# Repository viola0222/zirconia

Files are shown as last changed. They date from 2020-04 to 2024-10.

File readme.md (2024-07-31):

## 概要
___

「zirconia v.2.0」はマイクロマウスのチャンピオンが製作したオープンソースのマイクロマウスをnakagawaが改訂した版です。
 
詳しい説明は、[こちらのリンクの資料](https://docs.google.com/presentation/d/1BjXeR3dtw2jEZHByvPkCKbgB9d2WKhvbEWPhUpI-utg/edit?usp=sharing)を参照してください。
  
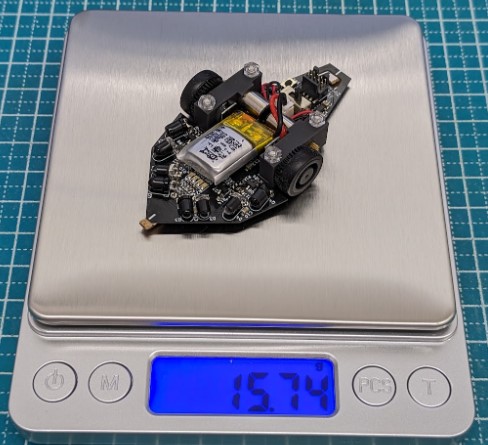
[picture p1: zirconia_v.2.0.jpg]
zirconia v.2.0


## 機能
___
 
各種インターフェースやセンサーの動作確認  

- マイコン各種機能(STM32F411)
- LED
- プッシュスイッチ
- モータ
- エンコーダ(MA730)
- IMU(ICM-42688-P)
- IRセンサ
  
機能の詳細についてはソフトマニュアルとサンプルコードのindex.hを参照して下さい。
 
## 動作環境
___
 
- 統合開発環境
    - STM32CubeIDE
    - Version :  1.15.0
    - URL : https://www.st.com/ja/development-tools/stm32cubeide.html
    - STM32CubeMX
    - Version :  6.10.0
    - URL : https://www.st.com/ja/development-tools/stm32cubemx.html    

- フラッシュライター
	- STM32CubeProgrammer
	- Version : 2.16.0
 	- URL : https://www.st.com/ja/development-tools/stm32cubeprog.html

※ Versionにはサンプルプログラムを開発したときのものを記載してあります。  
　　基本的には最新版をインストールすべきだと思いますが、  
　　サンプルプログラムが動かない等の不具合がありましたら参考にして下さい。

## 構成
___
 
- hardware
    - 回路図やガーバーデータ、部品リストなどハードウェアデータ
    - STEP 3D View https://a360.co/4cjsH3n
    
- software
    - CubeMXで自動生成したソフトと本サンプルプログラム
    - Incフォルダ内のIndex.hにサンプルプログラムの使い方が記載されています
    - Srcフォルダ内にmain.cなどのサンプルプログラムが入っています
- ハードマニュアル
    - ハードウェアの作り方や構成について記載されています
- ソフトマニュアル
    - サンプルプログラムの導入や使い方について記載されていますS
 
## その他
 ___

__本サンプルコードではマイクロマウスとして迷路を完走させることはできません。__  
本サンプルコードの目的は、製作したハードウェアの動作確認であり、その副産物として、マイクロマウスとして使いやすいデバイスドライバが書かれています。  
  
あくまでもzirconiaは動くハードウェアを用意しただけなので、ソフトウェアは自力で頑張れる人向けです。電子工作やプログラミングのガチ初心者にはオススメしません。  
電子工作や組み込みプログラム入門として、マイクロマウスを始める場合には(株)アールティより販売されている学習キット[Pi:Co Classic3.4 ESP32-S3](https://rt-net.jp/products/pico-classic3-esp32)や[Pi:Co V2](https://rt-net.jp/products/pico-v2)がオススメです。
 
## 作者
___
 
[Noriaki Nakagawa](https://github.com/noriakinakagawa)  
zirconia_sample is licensed under the Apache License, Version2.0

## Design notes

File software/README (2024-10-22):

# ビルド方法
## make

```bash
make
```

## clangd

- 次の内容の `compile_flags.txt` を作成することで、clangd による補完が動作するようになる

```
-I./arm-gnu-toolchain-13.2.Rel1-x86_64-arm-none-eabi/arm-none-eabi/include
```

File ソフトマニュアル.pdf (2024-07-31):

# 開発環境構築

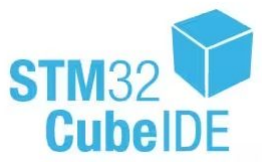
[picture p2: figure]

ま、下記ソフトをインストールしま。

① 統合開発環境

STM32CubeIDE

Version : 1.15.0

URL : https://www.st.com/ja/development-tools/stm32cubeide.html

② フラッシュライター

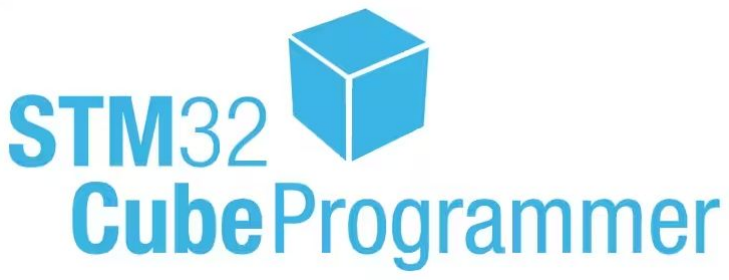
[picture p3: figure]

STM32CubeProgrammer

Version : 2.16.0

URL : https://www.st.com/ja/development-tools/stm32cubeprog.html

※ Versionサンプルプログラムを開発しきもを記載しありま。

基本的最新版をインストールべき思いまが、

サンプルプログラムが動かい等不具合がありましら参考し下さい。

# サンプルプログラムインポート

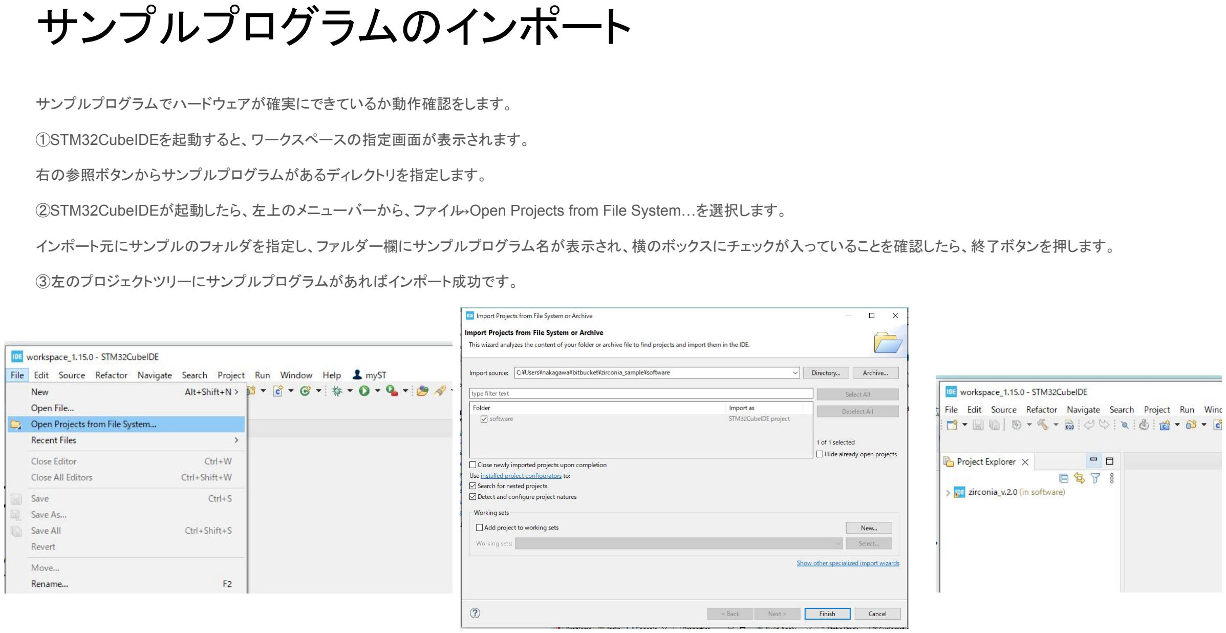
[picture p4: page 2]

サンプルプログラムハードウェアが確実きいるか動作確認をしま。

①STM32CubeIDEを起動る、ワークスペース指定画面が表示されま。

右参照ボタンからサンプルプログラムがあるディレクトリを指定しま。

②STM32CubeIDEが起動しら、左上メニューバーから、ファイル→Open Projects from File System…を選択しま。

インポート元サンプルフォルダを指定し、ファルダー欄サンプルプログラム名が表示され、横ボックスチェックが入いるこを確認しら、終了ボタンを押しま。

③左プロジェクトツリーサンプルプログラムがあれインポート成功。

# サンプルプログラムビルド

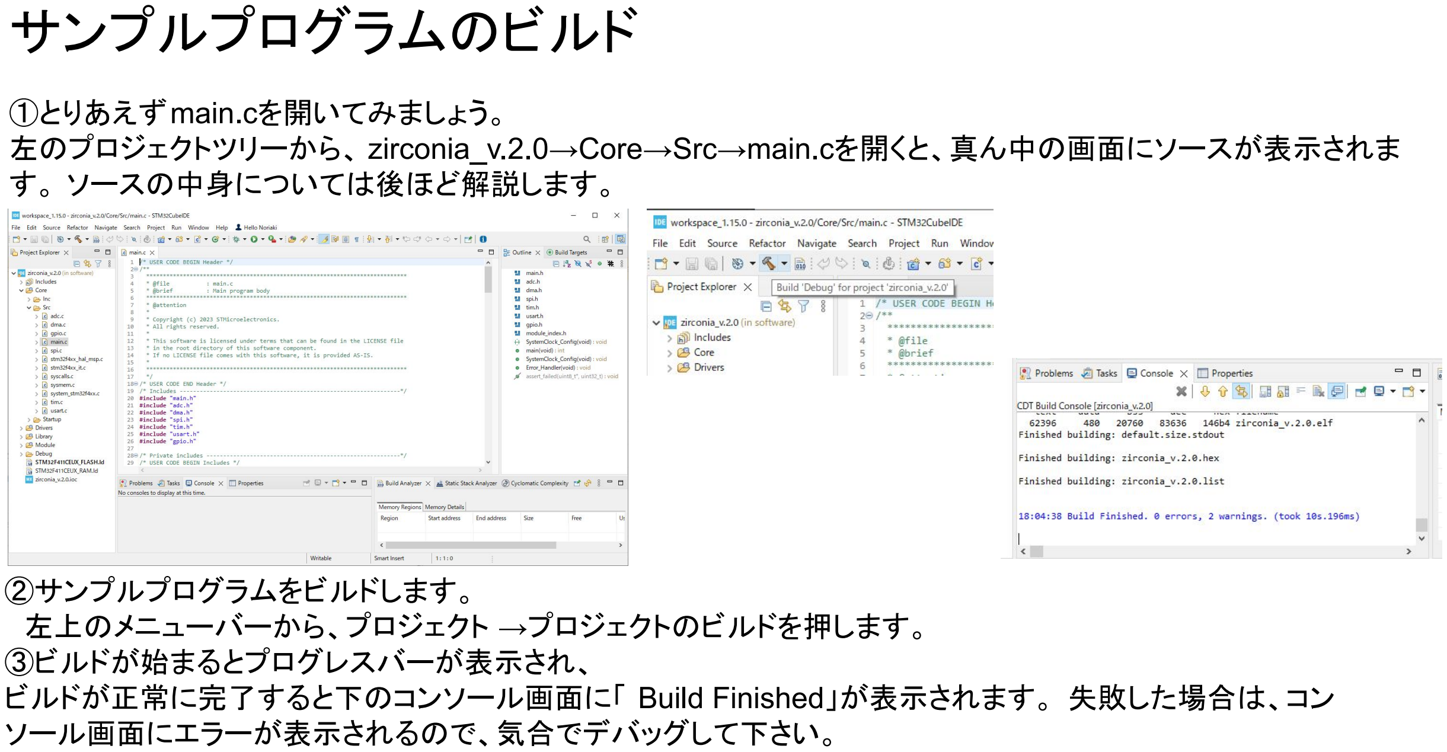
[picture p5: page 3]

①りあえmain.cを開いみましょう。
左プロジェクトツリーから、 zirconia_v.2.0→Core→Src→main.cを開く、真ん中画面ソースが表示されま 。 ソース中身い後ほ解説しま。

②サンプルプログラムをビルドしま。
左上メニューバーから、プロジェクト →プロジェクトビルドを押しま。 ③ビルドが始まるプログレスバーが表示され、
ビルドが正常完了る下コンソール画面「 Build Finished」が表示されま。 失敗し場合、コン ソール画面エラーが表示される、気合デバッグし下さい。

起動

①バッテリ通信ケーブルをマウス接続しま。
②電源スイッチをON側し電源を入れま。

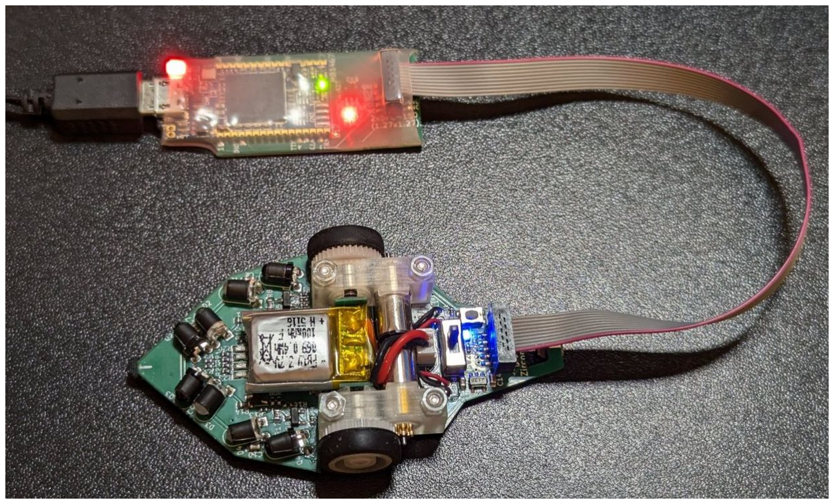
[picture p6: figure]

③電源スイッチ下青色 LEDが点灯しいれ、起動しいま。

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

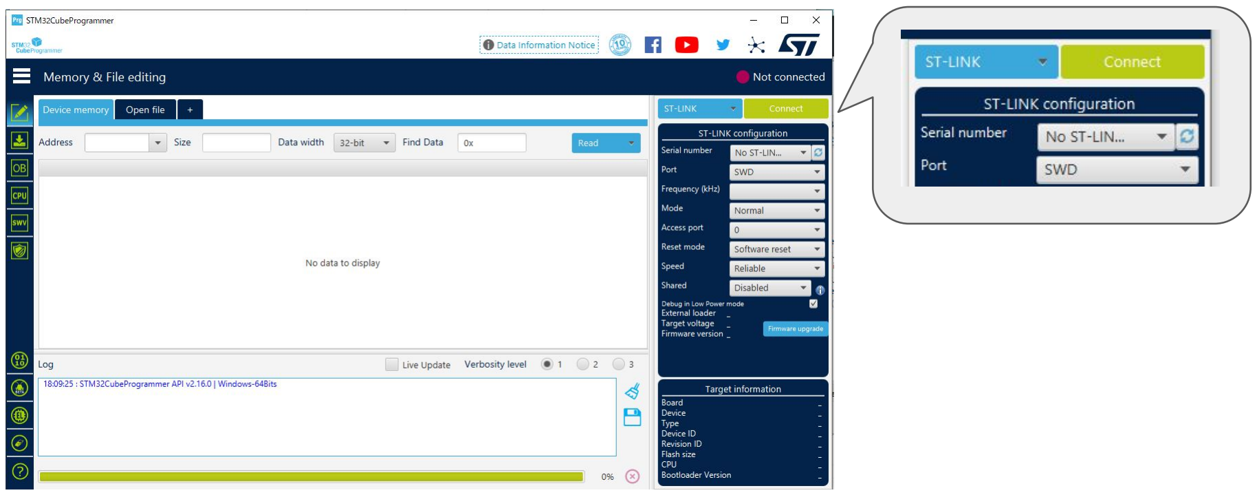
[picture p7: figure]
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

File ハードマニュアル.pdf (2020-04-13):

# Zirconia製作マニュアル

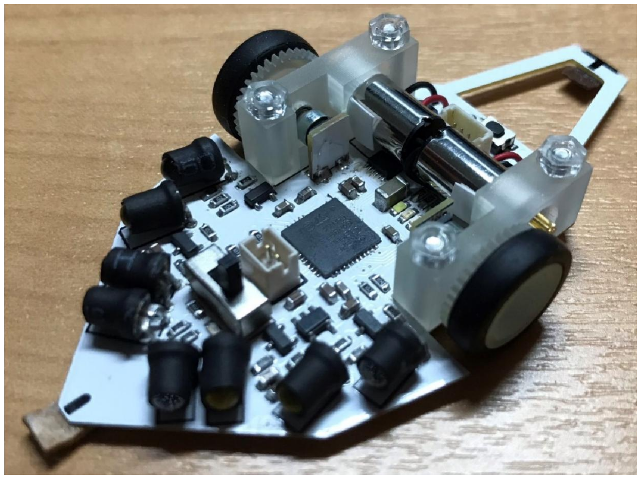
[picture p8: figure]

# Ver.0.0

(2019/1/27)

1

目次

## ■Ｐ３～５ 第１部：Ｚｉｒｃｏｎｉａの概要

・開発背景、コンセプト
・対象と開発スタート方法

## ■Ｐ７～１９ 第２部：機体の製作方法

・基板への電子部品の実装方法
・センサ類やケーブルの組み付け
・機構部品の組み立て
・モーターの組み付け

## ■Ｐ２０～？？ 第３部：ソフト書き込みと動作確認

・ソフト書き込み方法(電源投入、ケーブル接続、ソフト書き込み) ・動作確認方法(センサ、モーターの動作)
・まっすぐ前に進むための組み付け修正

## ■Ｐ？？～？？ 第４部：パラメータ調整方法？迷路走行？

・

2

## 開発背景

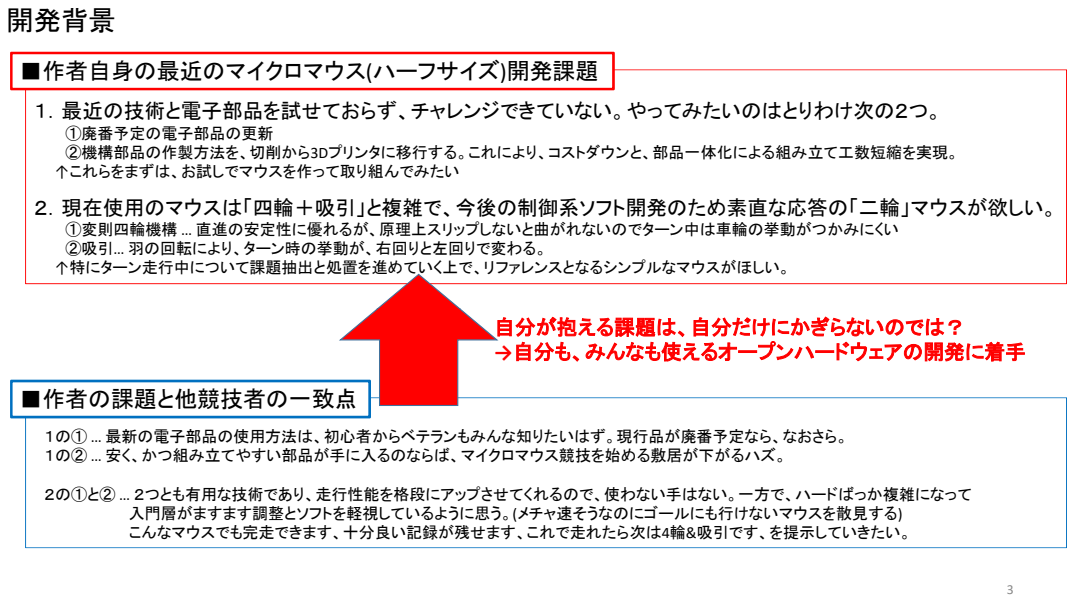
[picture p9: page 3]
自分が抱える課題は、自分だけにかぎらないのでは？ →自分も、みんなも使えるオープンハードウェアの開発に着手; ■作者の課題と他競技者の一致点

■作者自身の最近のマイクロマウス(ハーフサイズ)開発課題

１．最近の技術と電子部品を試せておらず、チャレンジできていない。やってみたいのはとりわけ次の２つ。
①廃番予定の電子部品の更新
②機構部品の作製方法を、切削から3Dプリンタに移行する。これにより、コストダウンと、部品一体化による組み立て工数短縮を実現。
↑これらをまずは、お試しでマウスを作って取り組んでみたい
２．現在使用のマウスは「四輪＋吸引」と複雑で、今後の制御系ソフト開発のため素直な応答の「二輪」マウスが欲しい。 ①変則四輪機構 … 直進の安定性に優れるが、原理上スリップしないと曲がれないのでターン中は車輪の挙動がつかみにくい

②吸引… 羽の回転により、ターン時の挙動が、右回りと左回りで変わる。
↑特にターン走行中について課題抽出と処置を進めていく上で、リファレンスとなるシンプルなマウスがほしい。

１の① … 最新の電子部品の使用方法は、初心者からベテランもみんな知りたいはず。現行品が廃番予定なら、なおさら。
１の② … 安く、かつ組み立てやすい部品が手に入るのならば、マイクロマウス競技を始める敷居が下がるハズ。

２の①と② … ２つとも有用な技術であり、走行性能を格段にアップさせてくれるので、使わない手はない。一方で、ハードばっか複雑になって

入門層がますます調整とソフトを軽視しているように思う。(メチャ速そうなのにゴールにも行けないマウスを散見する)
こんなマウスでも完走できます、十分良い記録が残せます、これで走れたら次は4輪&吸引です、を提示していきたい。

## コンセプト

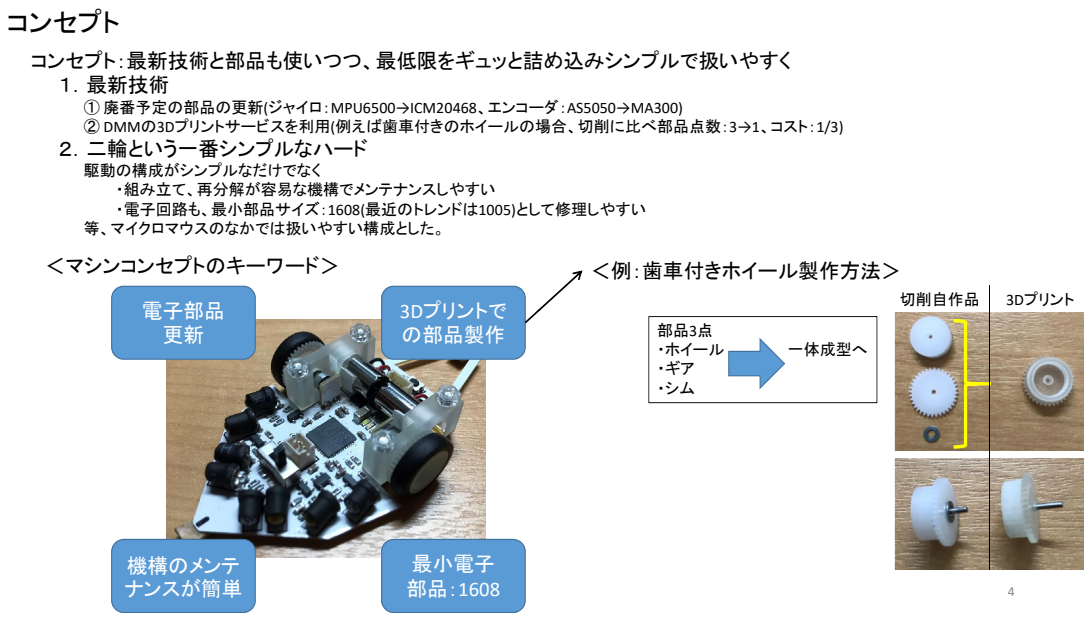
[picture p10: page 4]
切削自作品; 3Dプリント; ＜マシンコンセプトのキーワード＞; ＜例：歯車付きホイール製作方法＞; 電子部品; 3Dプリントで; ・ホイール; 一体成型へ; 電子部品 更新; 3Dプリントで の部品製作; 機構のメンテ ナンスが簡単; 最小電子 部品：1608

コンセプト：最新技術と部品も使いつつ、最低限をギュッと詰め込みシンプルで扱いやすく
１．最新技術
① 廃番予定の部品の更新(ジャイロ：MPU6500→ICM20468、エンコーダ：AS5050→MA300)
② DMMの3Dプリントサービスを利用(例えば歯車付きのホイールの場合、切削に比べ部品点数：3→1、コスト：1/3)
２．二輪という一番シンプルなハード
駆動の構成がシンプルなだけでなく
・組み立て、再分解が容易な機構でメンテナンスしやすい
・電子回路も、最小部品サイズ：1608(最近のトレンドは1005)として修理しやすい
等、マイクロマウスのなかでは扱いやすい構成とした。

## 対象者とおススメの開発スタート方法

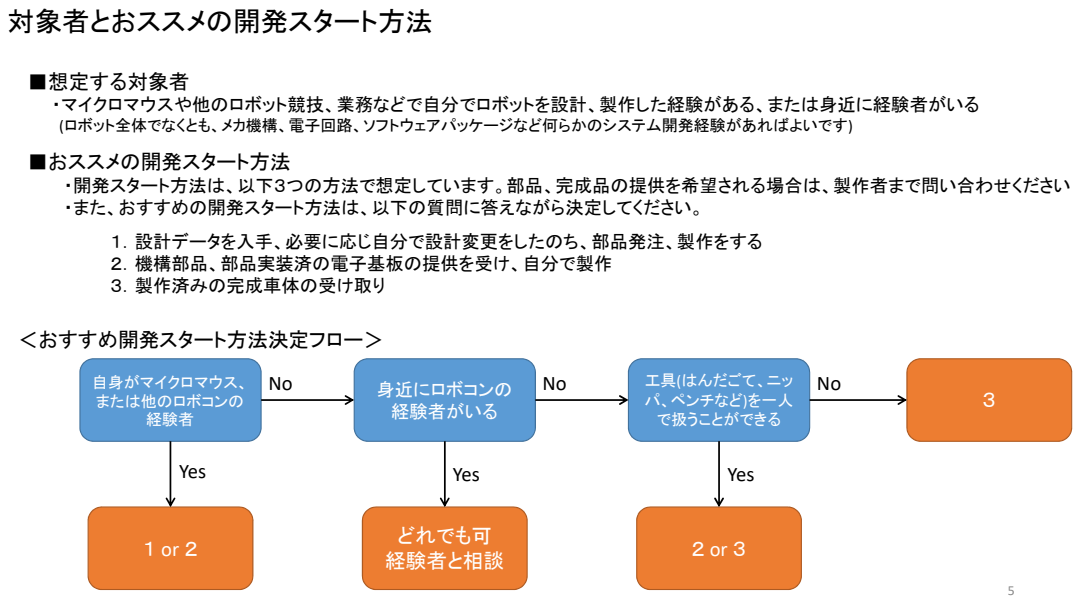
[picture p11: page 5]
自身がマイクロマウス、 または他のロボコンの 経験者; 身近にロボコンの; 経験者がいる; どれでも可; 経験者と相談; Yes; ＜おすすめ開発スタート方法決定フロー＞

■想定する対象者
・マイクロマウスや他のロボット競技、業務などで自分でロボットを設計、製作した経験がある、または身近に経験者がいる
(ロボット全体でなくとも、メカ機構、電子回路、ソフトウェアパッケージなど何らかのシステム開発経験があればよいです)
■おススメの開発スタート方法
・開発スタート方法は、以下３つの方法で想定しています。部品、完成品の提供を希望される場合は、製作者まで問い合わせください
・また、おすすめの開発スタート方法は、以下の質問に答えながら決定してください。
１．設計データを入手、必要に応じ自分で設計変更をしたのち、部品発注、製作をする
２．機構部品、部品実装済の電子基板の提供を受け、自分で製作
３．製作済みの完成車体の受け取り

工具(はんだごて、ニッ
パ、ペンチなど)を一人
で扱うことができる

# 以降、製作方法説明

6

## 面実装電子部品の実装(表面)

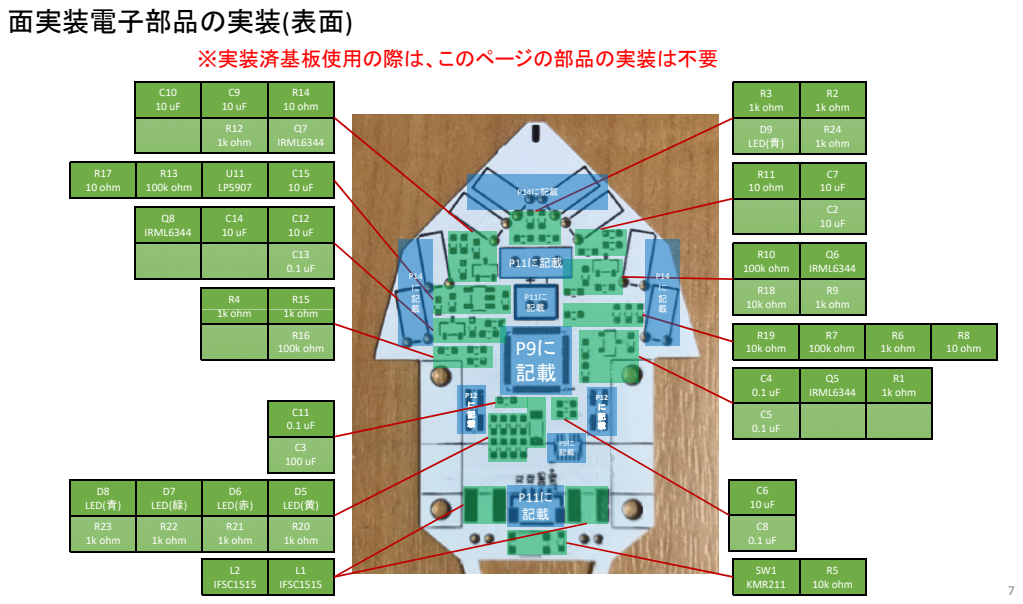
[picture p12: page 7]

## 面実装電子部品の実装(サブボード、裏面)

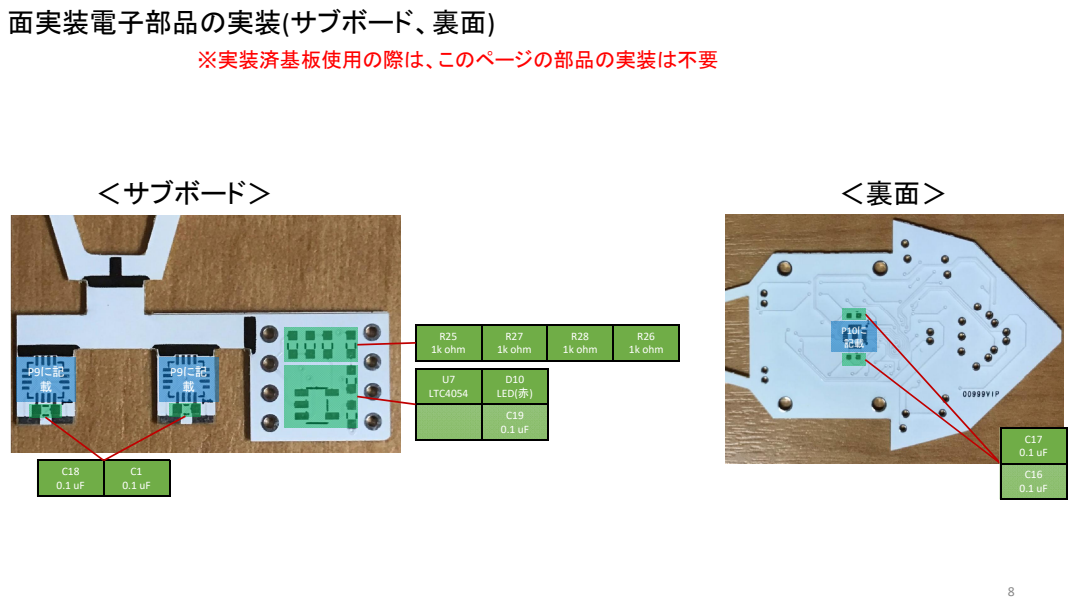
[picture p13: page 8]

U7 LTC4054 | D10 LED(赤)

## 向きのある電子部品の実装向き(表面)

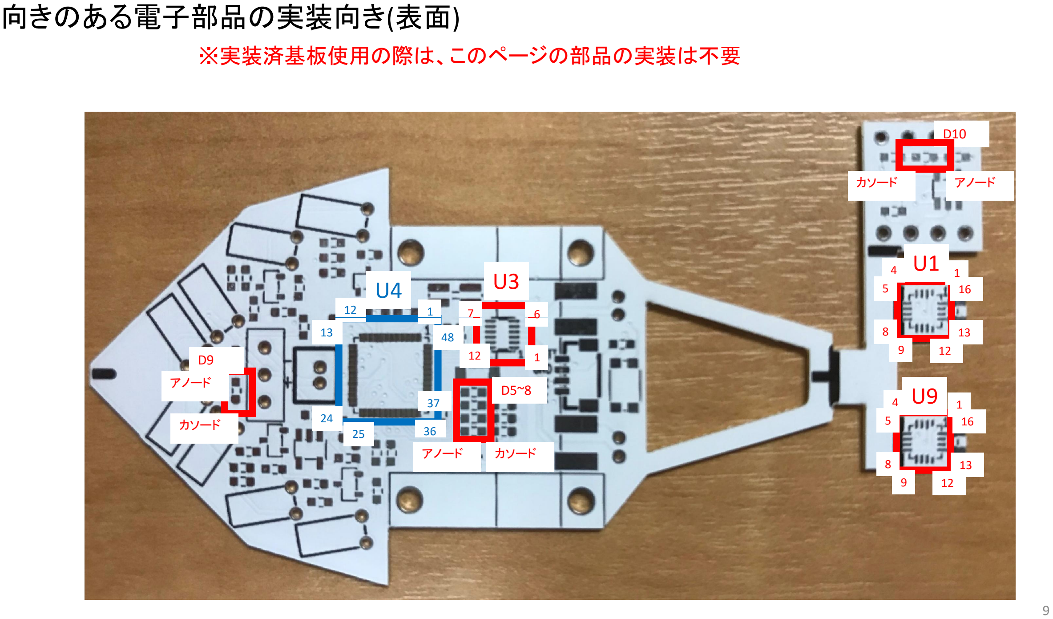
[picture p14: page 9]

U3

7 | 6

D10

カソード | アノード

U4

12 | 1
4 | U1 | 1
5 | 16

※実装済基板使用の際は、このページの部品の実装は不要

9

1

6

12

アノード カソード

D5~8

D9

カソード

アノード

13

24
25 | 36
| 37

48

U9

8
9 12

13

4 | 1
5

8
9 12

13

16

## 向きのある電子部品の実装向き(裏面)

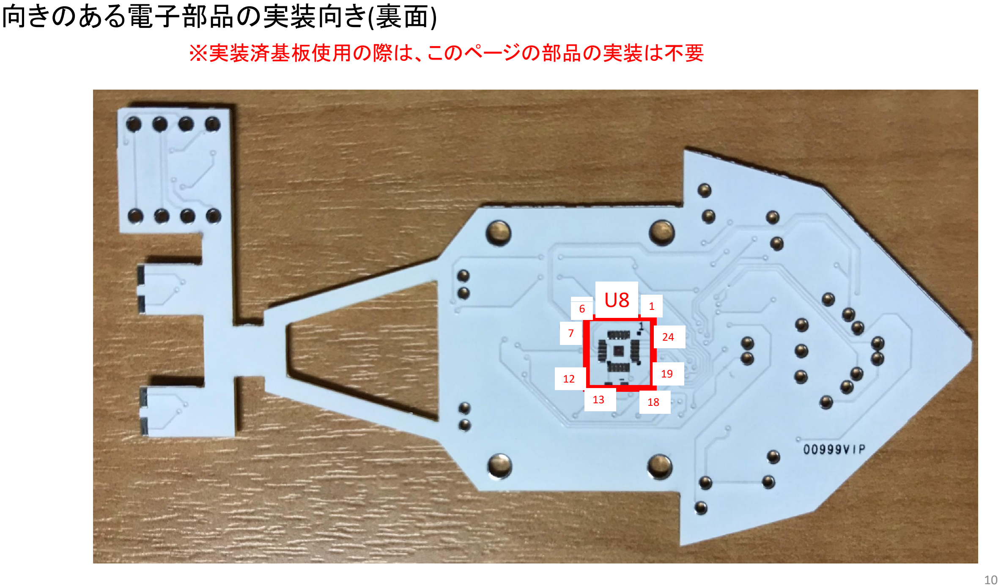
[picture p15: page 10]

U8

※実装済基板使用の際は、このページの部品の実装は不要

10

6 | U8 | 1

7

12

13 | 18

19

24

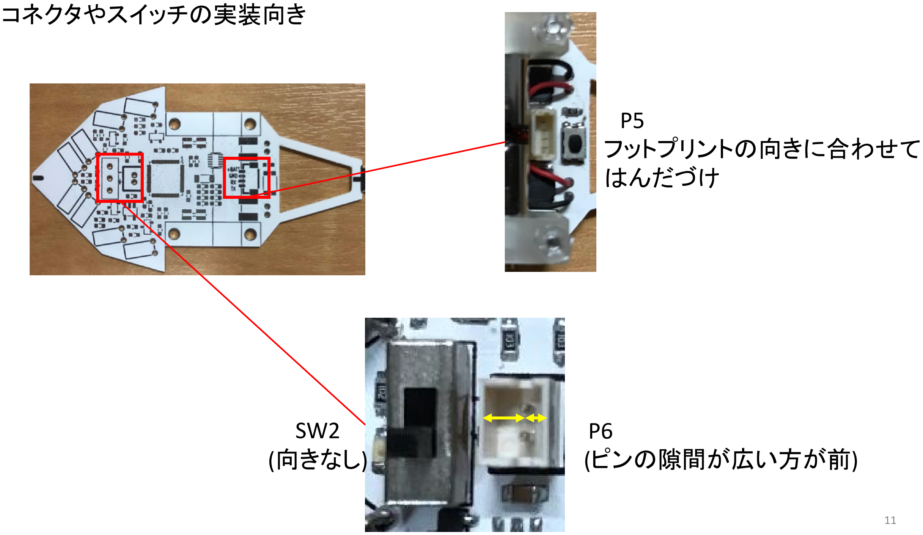
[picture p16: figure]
コネクタやスイッチの実装向き; P5 フットプリントの向きに合わせて はんだづけ; SW2 (向きなし); P6 (ピンの隙間が広い方が前)

## エンコーダ―の組付け方

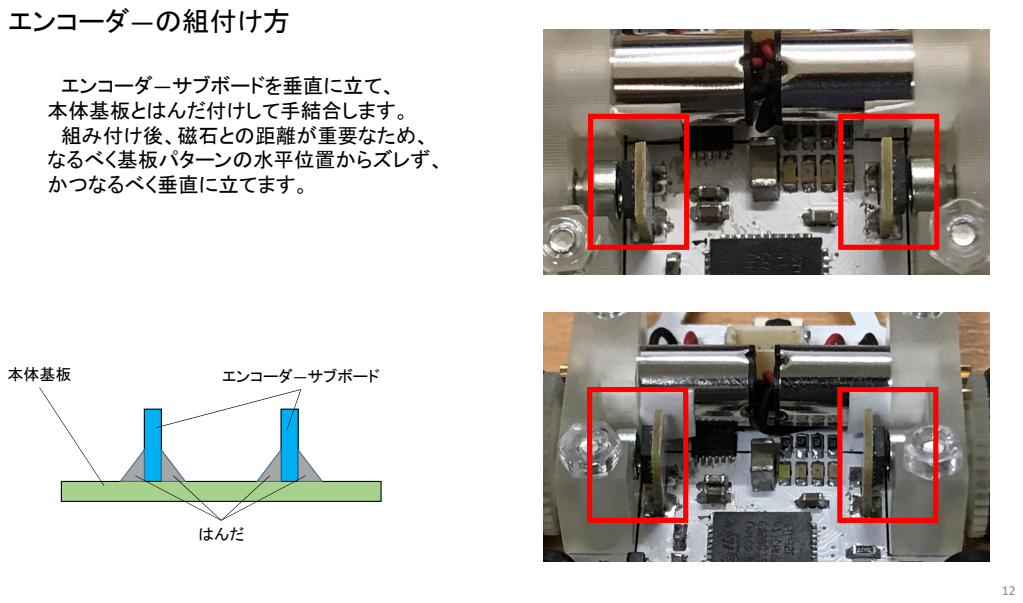
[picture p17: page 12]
エンコーダ―サブボードを垂直に立て、 本体基板とはんだ付けして手結合します。 組み付け後、磁石との距離が重要なため、 なるべく基板パターンの水平位置からズレず、 かつなるべく垂直に立てます。; 本体基板; エンコーダ―サブボード; はんだ

## 充電、通信ケーブルの組み立て方

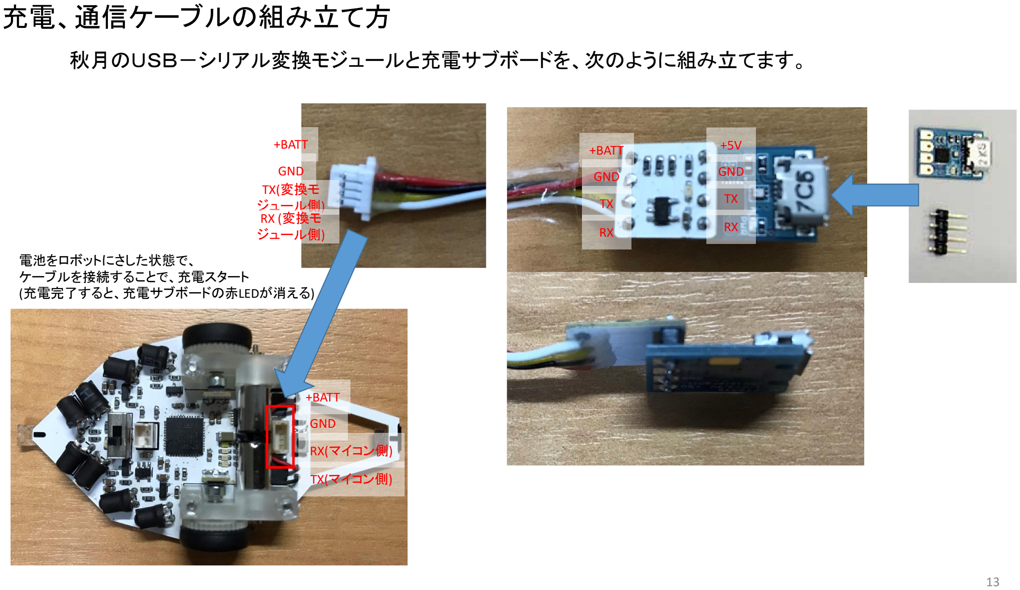
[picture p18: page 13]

秋月のＵＳＢ－シリアル変換モジュールと充電サブボードを、次のように組み立てます。

+5V

GND

TX

RX

+BATT

GND

TX

RX

+BATT

GND
TX(変換モ
ジュール側)
RX (変換モ
ジュール側)

電池をロボットにさした状態で、
ケーブルを接続することで、充電スタート
(充電完了すると、充電サブボードの赤LEDが消える)

13

+BATT

GND

RX(マイコン側)

TX(マイコン側)

## センサの組み付け

①LED(D1~D4)の足を、左側に足の長いほうが来るように曲げます ②LEDの樹脂部分の側面を覆うように、黒いビニールテープを巻きます。 (LEDの光がフォトトランジスタ(Q1~Q4)に届かないようにするためです) ③基板の穴に挿入し、はんだ付けします。
④フォトトランジスタも同様にします。(曲げるときの長い脚の向きは、同じです。)
＜①LEDを曲げる＞ | ＜①の参考：曲げる向き＞ | ＜②黒ビニテ貼り＞

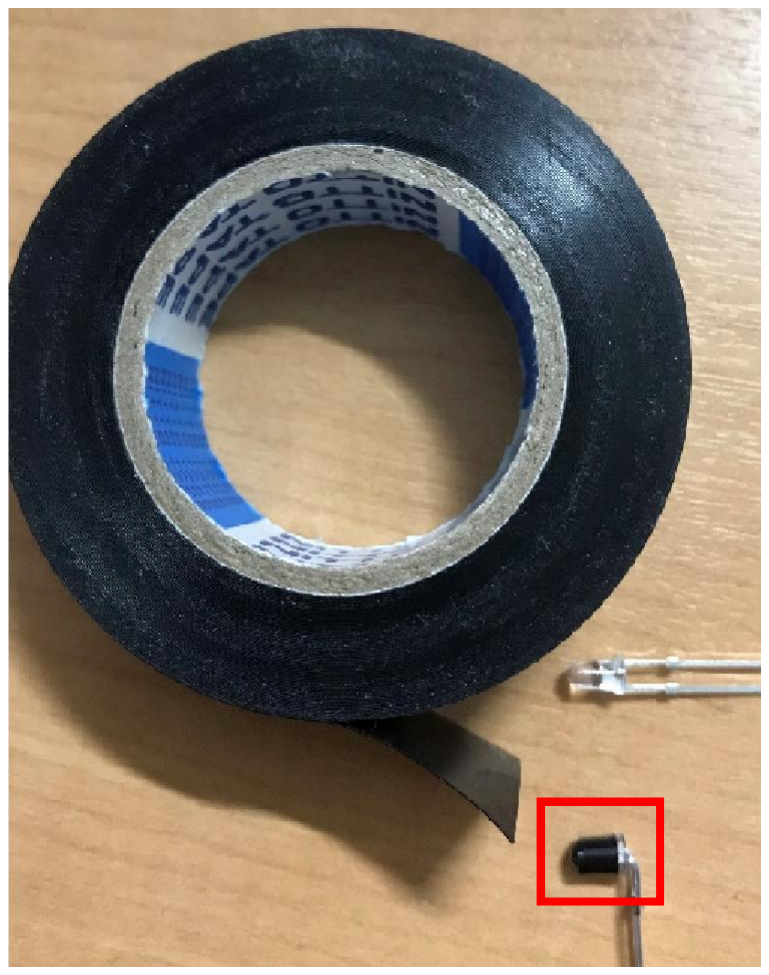
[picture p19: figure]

14

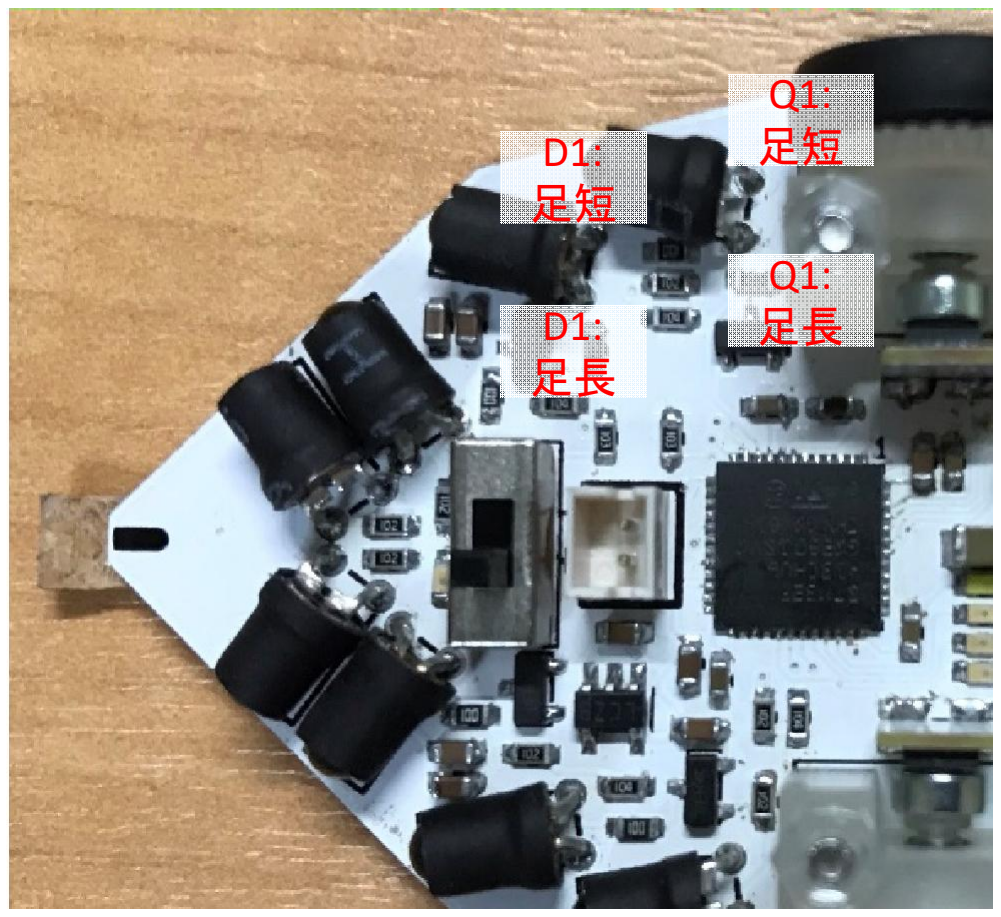
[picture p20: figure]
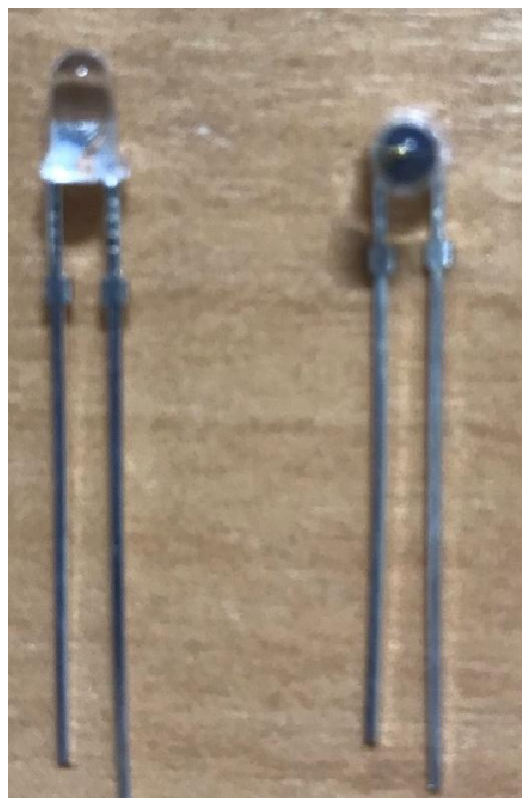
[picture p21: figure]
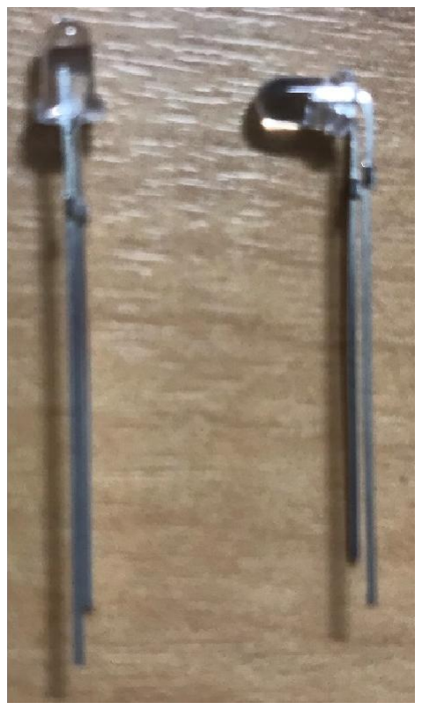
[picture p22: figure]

## バッテリの組み付け

＋とGND確認してはんだ付け、ショート注意

15

## はじめに次の3つを準備します。 これを、以下の断面図に沿って組み立てます。

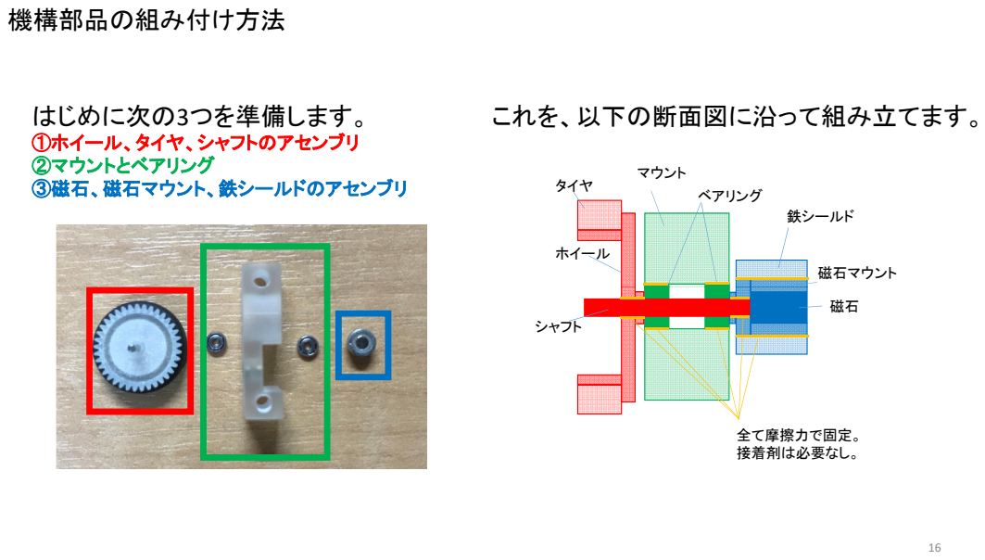
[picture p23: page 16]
タイヤ; ホイール; マウント; ベアリング; 鉄シールド; 磁石マウント; 機構部品の組み付け方法; シャフト; 全て摩擦力で固定。 接着剤は必要なし。

①ホイール、タイヤ、シャフトのアセンブリ
②マウントとベアリング
③磁石、磁石マウント、鉄シールドのアセンブリ

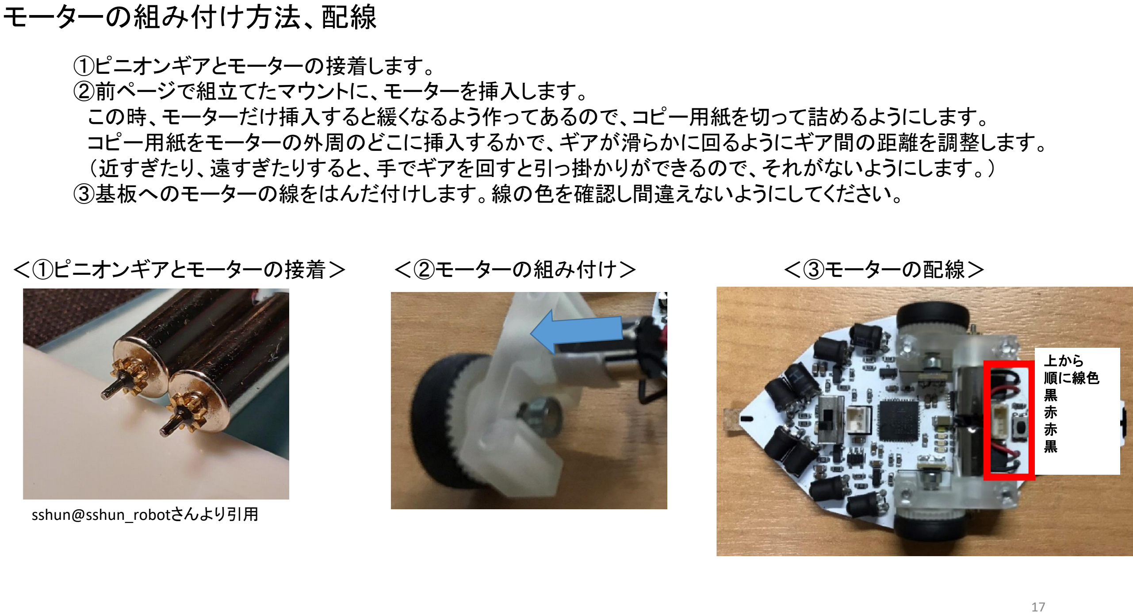
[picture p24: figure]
モーターの組み付け方法、配線; ＜①ピニオンギアとモーターの接着＞; ①ピニオンギアとモーターの接着します。 ②前ページで組立てたマウントに、モーターを挿入します。 この時、モーターだけ挿入すると緩くなるよう作ってあるので、コピー用紙を切って詰めるようにします。 コピー用紙をモーターの外周のどこに挿入するかで、ギアが滑らかに回るようにギア間の距離を調整します。 （近すぎたり、遠すぎたりすると、手でギアを回すと引っ掛かりができるので、それがないようにします。） ③基板へのモーターの線をはんだ付けします。線の色を確認し間違えないようにしてください。; ＜②モーターの組み付け＞; ＜③モーターの配線＞; sshun@sshun_robotさんより引用; 上から 順に線色 黒 赤 赤 黒

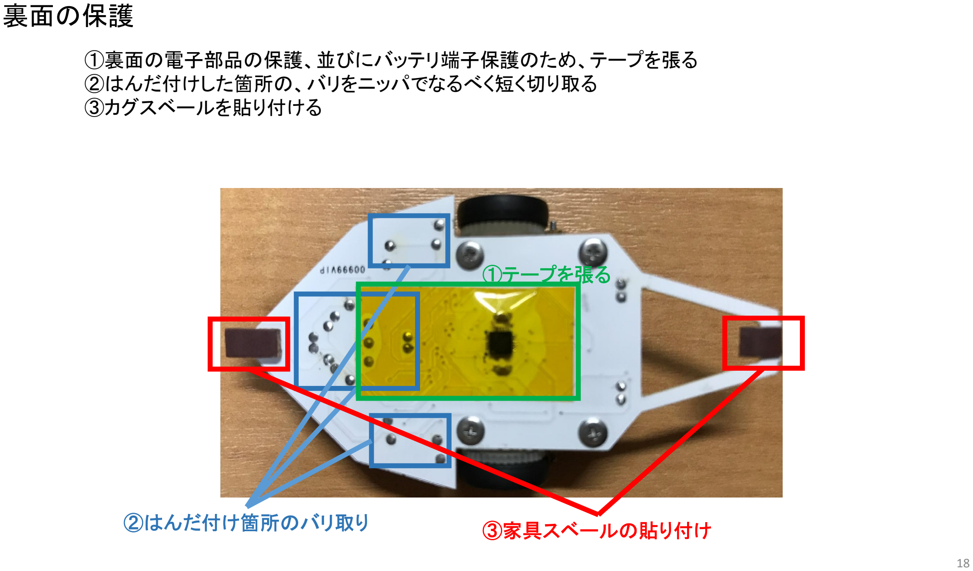
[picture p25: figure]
裏面の保護; ①裏面の電子部品の保護、並びにバッテリ端子保護のため、テープを張る ②はんだ付けした箇所の、バリをニッパでなるべく短く切り取る ③カグスベールを貼り付ける; ①テープを張る; ②はんだ付け箇所のバリ取り; ③家具スベールの貼り付け

完成！


19

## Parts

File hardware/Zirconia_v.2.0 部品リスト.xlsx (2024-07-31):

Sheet: 手配部品リスト(ベアリングホルダー方式)
大分類 | 品目 | 品名/型番 | 入手先 | 個数 | 参考URL | 参考価格(税込)
機構部品 | ピニオンギア | 精密切削ピニオンギヤ(m0.3 T9 2mm) 2個入り | RT | 2 | https://www.rt-shop.jp/index.php?main_page=product_info&cPath=1002_1024_1283&products_id=2984 | 880
 | モーター | コアレスモータ NFP-D0612 (2個入) | RT | 2 | https://www.rt-shop.jp/index.php?main_page=product_info&products_id=4156 | 1100
 | タイヤ | マイクロマウス用タイヤ10度 10個入り | RT | 2 | https://www.rt-shop.jp/index.php?main_page=product_info&products_id=3642 | 2200
 | カグスベール | ニチアス カグスベール フリーサイズ 1シート 茶 321230 | amazon | 1 | https://amzn.asia/d/05YCirS | 660
 | 磁石 | ネオジム磁石(N40)、円柱型、Φ3x2(mm)、径方向 | ネオマグ | 2 | https://www.neomag.jp/shop/shoppingcart/itemdetail.php?itemno=MAG17163612992482&qty=1 | 98
 | 3Dプリンタ部品 | DMMの3Dプリントサービス 材質は高精細アクリル｜MJT｜3500HDMax hardware/ZirconiaSTL_v.2.0.stl | DMM.make | 1 | https://make.dmm.com/mypage/upload/ | 3621
 | 平ギヤ | Gearwheel Pinion M0.3 / 38teeth OD 12mm drill3mm、width1.5、Polyaceetal POM white | kkpmo | 2 | https://shop.kkpmo.com/product_info.php?info=p400_gearwheel-pinion-m0-3---38teeth-od-12mm.html | 2232.1
 | ベアリング | ベアリング外径6内径3厚2.5 MR63ZZ | モノタロウ | 4 | https://www.monotaro.com/p/8892/7027/ | 876
 | ネジ | (+)スリムヘッド小ねじ (ステンレス)(パック品) 低頭M2-10 | モノタロウ | 4 | https://www.monotaro.com/p/4174/6731/?t.q=%92%B4%92%E1%93%AA%83l%83W%20m2 | 450
 | ナット | M 2 六角ナット(ポリカーボネート/10個) | モノタロウ | 4 | https://www.monotaro.com/g/02444870/?t.q=%83i%83b%83g%20m2 | 495
 | 平行ピン | 3x8 平行ピン 硬質(ステンレス) | モノタロウ | 2 | https://www.monotaro.com/p/4220/5283/?fem1=1 | 439
 | シムリング | 3×4mm セットアップ・ステンレスシム 0.1/0.2/0.3mm厚 各10枚入 [EG-SH3] | スーパーラジコン | 1 | https://super-rc.co.jp/rc/product/view?id=30206 | 347
未実装電子部品 | バッテリ(4つのうちどれか1つでOK) | 100mAhリチウム電池モデルバッテリーSYMA X12S用 | amazon |  | https://amzn.asia/d/fZSeMQ6 | 277
 | バッテリ(4つのうちどれか1つでOK) | Tygzs M1 KFPLAN KF606蒸気RC飛行機のための1S 3.7V 50mAhミニリポ電池モレックス2P 1.25mmコネクタ1cm 4g | Banggood | 1 | https://jp.banggood.com/1S-3_7V-50mAh-Mini-LiPo-Battery-Molex-2P-1_25mm-Connector-1cm-4g-For-Tygzs-M1-KFPLAN-KF606-Vapor-RC-Airplane-p-1381041.html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
 | バッテリ(4つのうちどれか1つでOK) | 100mAh ミニrcクワッドコプター用 ※コネクタがついてない場合あり | Aliexpress | 1 | https://ja.aliexpress.com/item/1005002596506305.html
 | バッテリ(4つのうちどれか1つでOK) | 3.7V 100mAh リポバッテリー | amazon | 1 | https://amzn.asia/d/j8ljUXm
 | バッテリコネクタ(P6) | PicoBlade 530470210 | Digikey | 1 | https://www.digikey.jp/short/10232fr3 | 41.8
 | 磁気式エンコーダ(U1, U9) | MA730GQ-Z or MA302GQ-Z | Digikey | 2 | https://www.digikey.jp/short/b3m30fzz | 2076.8
 | ST-LINK(U12) | STLINK-V3MODS or AE-FT234X | Digikey | 1 | https://www.digikey.jp/short/mr74wj20 | 1444
 | 壁センサ受光素子(Q1～4) | LTR-4206E | Digikey | 4 | https://www.digikey.jp/product-detail/ja/lite-on-inc/LTR-4206E/160-1030-ND/121710 | 281.6
 | ピンヘッダ2x5(J1, J4) | ピンヘッダ 2×5(10P) 表面実装用 1.27mmピッチ | akiduki | 2 | https://akizukidenshi.com/catalog/g/g110904/ | 60
 | 壁センサLED(D1~4) | OSI5FU3A11C | akiduki | 4 | http://akizukidenshi.com/catalog/g/gI-04313/ | 200
 | 電源スイッチ(SW2) | SS12D01G4 | akiduki | 1 | http://akizukidenshi.com/catalog/g/gP-12723/ | 25
ハーネス | 充電、通信ハーネス(P8) | 2×5(10P)両端コネクタ付IDCリボンケーブル(フラットケーブル ハーフピッチ) | akiduki | 1 | https://akizukidenshi.com/catalog/g/g106776/ | 240
 | USBケーブル microB | 通信ができるタイプなら何でもOK | akiduki | 1 | https://akizukidenshi.com/catalog/g/g117016/ | 90
その他準備品 | ドライバー0番
 | はんだごて(20～30W)、先が細いもの
 | セロハンテープ、できればカプトンテープ
 | エポキシ系接着剤 | 例えば、コニシのボンドクイック5
 | 難接着材料用接着剤ＰＰＸ |  |  |  | https://www.cemedine.co.jp/home/adhesive/polyolefin/index.html
 | アロンアルファ
 |  |  |  |  |  | 18134.3
参考資料 | マイクロマウス合宿2023 Mice Busters なおフィス マイクロマウスの足回りについて ソフト屋さんが考えるシンプルな足回りの紹介

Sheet: 手配部品リスト(zirconia v.1.0方式)
大分類 | 品目 | 品名/型番 | 入手先 | 個数 | 参考URL | 参考価格(税込)
機構部品 | ピニオンギア | 精密切削ピニオンギヤ(m0.3 T9 2mm) 2個入り | RT | 2 | https://www.rt-shop.jp/index.php?main_page=product_info&cPath=1002_1024_1283&products_id=2984 | 880
 | モーター | コアレスモータ NFP-D0612 (2個入) | RT | 2 | https://www.rt-shop.jp/index.php?main_page=product_info&products_id=4156 | 1100
 | タイヤ | マイクロマウス用タイヤ10度 10個入り | RT | 2 | https://www.rt-shop.jp/index.php?main_page=product_info&products_id=3642 | 2200
 | カグスベール | ニチアス カグスベール フリーサイズ 1シート 茶 321230 | amazon | 1 | https://amzn.asia/d/05YCirS | 660
 | 磁石 | ネオジム磁石(N40)、円柱型、Φ3x2(mm)、径方向 | ネオマグ | 2 | https://www.neomag.jp/shop/shoppingcart/itemdetail.php?itemno=MAG17163612992482&qty=1 | 98
 | 3Dプリンタ部品 | DMMよりDMMpartsZirconiaをダウンロードし、発注する 材質はアクリル（Xtreme Mode） | DMM.make | 1 | https://make.dmm.com/item/918432/ | 4831
 | 鉄スペーサー | スペーサー(スチールスペーサー) CF-2600ZEシリーズ(M=2.6用) | モノタロウ | 2 | https://www.monotaro.com/g/01213381/?t.attr_f3439=%83X%83%60%81%5B%83%8B
 | ベアリング | DDL-310 | モノタロウ | 4 | https://www.monotaro.com/p/0953/8094/ | 876
 | ネジ | (+)スリムヘッド小ねじ (ステンレス)(パック品) | モノタロウ | 4 | https://www.monotaro.com/p/4174/6731/?t.q=%92%B4%92%E1%93%AA%83l%83W%20m2 | 450
 | ナット | M 2 六角ナット(ポリカーボネート/10個) | モノタロウ | 4 | https://www.monotaro.com/g/02444870/?t.q=%83i%83b%83g%20m2 | 495
 | 平行ピン | 平行ピン | モノタロウ | 2 | https://www.monotaro.com/p/4220/4741/ | 439
未実装電子部品 | バッテリ | Tygzs M1 KFPLAN KF606蒸気RC飛行機のための1S 3.7V 50mAhミニリポ電池モレックス2P 1.25mmコネクタ1cm 4g | Banggood | 1 | https://jp.banggood.com/1S-3_7V-50mAh-Mini-LiPo-Battery-Molex-2P-1_25mm-Connector-1cm-4g-For-Tygzs-M1-KFPLAN-KF606-Vapor-RC-Airplane-p-1381041.html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 | 1425
 | バッテリ | Li-Po 50mAh 幅15mm以内 | amazon | 1 | https://www.amazon.co.jp/s?k=50mAh
 | バッテリコネクタ(P6) | PicoBlade 530470210 | Digikey | 1 | https://www.digikey.jp/short/10232fr3 | 41.8
 | 磁気式エンコーダ(U1, U9) | MA730GQ-Z or MA302GQ-Z | Digikey | 2 | https://www.digikey.jp/short/b3m30fzz | 2076.8
 | ST-LINK(U12) | STLINK-V3MODS or AE-FT234X | Digikey | 1 | https://www.digikey.jp/short/mr74wj20 | 1444
 | 壁センサ受光素子(Q1～4) | LTR-4206E | Digikey | 4 | https://www.digikey.jp/product-detail/ja/lite-on-inc/LTR-4206E/160-1030-ND/121710 | 281.6
 | ピンヘッダ2x5(J1, J4) | ピンヘッダ 2×5(10P) 表面実装用 1.27mmピッチ | akiduki | 2 | https://akizukidenshi.com/catalog/g/g110904/ | 60
 | 壁センサLED(D1~4) | OSI5FU3A11C | akiduki | 4 | http://akizukidenshi.com/catalog/g/gI-04313/ | 200
 | 電源スイッチ(SW2) | SS12D01G4 | akiduki | 1 | http://akizukidenshi.com/catalog/g/gP-12723/ | 25
ハーネス | 充電、通信ハーネス(P8) | 2×5(10P)両端コネクタ付IDCリボンケーブル(フラットケーブル ハーフピッチ) | akiduki | 1 | https://akizukidenshi.com/catalog/g/g106776/ | 240
 | USBケーブル microB | 通信ができるタイプなら何でもOK | akiduki | 1 | https://akizukidenshi.com/catalog/g/g117016/ | 90
その他準備品 | ドライバー0番
 | はんだごて(20～30W)、先が細いもの
 | セロハンテープ、できればカプトンテープ
 | エポキシ系接着剤 | 例えば、コニシのボンドクイック5
 | アロンアルファ
 |  |  |  |  |  | 17913.2

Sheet: 実装BOM_JLCPCB在庫部品一部構成
品名（Name） | 部品番号（Designator） | 個数（Quantity） | 値（Value） | パッケージ（Package） | 説明（Description） | 部品メーカー（Manufacturer） | 部品メーカーの型番（Manufacturer Part Number） | 代替可否 | Link
セラミックコンデンサ | C1, C4, C5, C8, C11, C13, C16, C18, C19 | 9 | 0.1uF 16V | 表面実装1005mm |  | Samsung Electro-Mechanics | CL05B104KP5NNNC | 可 | https://www.digikey.jp/short/mcf590zw
セラミックコンデンサ | C2, C6, C7, C9, C10, C12, C14, C15, C20, C21 | 10 | 10uF 25V | 表面実装1608mm |  | Samsung Electro-Mechanics | CL10A106MA8NRNC | 可 | https://www.digikey.jp/short/77w877jb
セラミックコンデンサ | C17 | 1 | 10nF | 表面実装1005mm |  | Murata Electronics | GCM155R71H103KA55D | 可 | https://www.digikey.jp/short/4n2p0070
ＬＥＤ | D1, D3 | 2 | OSI5FU3A11C |  | 向きがあるので、実装注意 (本ファイル別タブ「部品実装向き」参照) | OptoSupply | OSI5FU3A11C | 不可 | https://akizukidenshi.com/catalog/g/g104313/
ＬＥＤ | D2, D4 | 2 | OSI5FU3A11C | D1,D3と曲げ向き逆 | 向きがあるので、実装注意 (本ファイル別タブ「部品実装向き」参照) | OptoSupply | OSI5FU3A11C | 不可 | https://akizukidenshi.com/catalog/g/g104313/
ＬＥＤ | D5 | 1 | Yellow | 表面実装1608mm | 向きがあるので、実装注意 (本ファイル別タブ「部品実装向き」参照) | Broadcom Limited | XL-1608UYC-06 | 可 | https://jlcpcb.com/partdetail/Xinglight-XL_1608UYC06/C965802
ＬＥＤ | D6, D10 | 2 | Red | 表面実装1608mm | 向きがあるので、実装注意 (本ファイル別タブ「部品実装向き」参照) | Broadcom Limited | XL-1608SURC-06 | 可 | https://jlcpcb.com/partdetail/Xinglight-XL_1608SURC06/C965799
ＬＥＤ | D7 | 1 | Green | 表面実装1608mm | 向きがあるので、実装注意 (本ファイル別タブ「部品実装向き」参照) | Broadcom Limited | XL-1608SYGC-06 | 可 | https://jlcpcb.com/partdetail/Xinglight-XL_1608UBC04/C965807
ＬＥＤ | D8, D9 | 2 | Blue | 表面実装1608mm | 向きがあるので、実装注意 (本ファイル別タブ「部品実装向き」参照) | Broadcom Limited | XL-1608UBC-04 | 可 | https://jlcpcb.com/partdetail/Xinglight-XL_1608UBC04/C965807
コネクタ | J1, J4 | 2 | X1321WVS-2x05J-C40D53 |  | 向きがあるので、実装注意 (本ファイル別タブ「部品実装向き」参照) | XKB Connection | X1321WVS-2x05J-C40D53 | 可 | https://jlcpcb.com/partdetail/XkbConnection-X1321WVS_2x05JC40D53/C2881910
インダクタ | L1, L2 | 2 | 47uH | 表面実装4.00mm x 4.00mm |  | cjiang | AMWPH4018S470MT | 可 | https://jlcpcb.com/partdetail/Sunlord-AMWPH4018S470MT/C2846193
コネクタ | P6 | 1 | PicoBlade 530470210 |  | 向きがあるので、実装注意 (本ファイル別タブ「部品実装向き」参照) | Molex | 530470210 | 不可 | https://www.digikey.jp/short/wvd5808v
フォトトランジスタ | Q1, Q2 | 2 | LTR |  | 向きがあるので、実装注意 (本ファイル別タブ「部品実装向き」参照) | Lite-On Inc. | LTR-4206E | 不可 | https://www.digikey.jp/short/5j5rwn2h
フォトトランジスタ | Q3, Q4 | 2 | LTR | Q1,Q2と曲げ向き逆 | 向きがあるので、実装注意 (本ファイル別タブ「部品実装向き」参照) | Lite-On Inc. | LTR-4206E | 不可 | https://www.digikey.jp/short/5j5rwn2h
ＭＯＳＦＥＴ | Q5, Q6, Q7, Q8 | 4 | IRLML6344 | SOT-23-3 |  | Infineon Technologies | IRLML6344TRPBF | 不可 | https://www.digikey.jp/short/2wcnthqm
ＭＯＳＦＥＴ | Q9 | 1 | DMC2400UV-7 | SOT-563 | 向きがあるので、実装注意 (本ファイル別タブ「部品実装向き」参照) | Diodes Incorporated | DMC2400UV-7 | 可 | https://www.digikey.jp/short/p1drtvbm
抵抗 | R1, R2, R3, R4, R6, R9, R12, R15, R20, R21, R23, R24, R26, R27, R28 | 16 | 1k Ohms | 表面実装1005mm |  | YAGEO | RC0402FR-071KL | 可 | https://www.digikey.jp/short/82nrqjd4
抵抗 | R5, R18, R19, R25 | 3 | 10k Ohms | 表面実装1005mm |  | Samsung Electro-Mechanics | RC1005F103CS | 可 | https://www.digikey.jp/short/rj3rq8wd
抵抗 | R7, R10, R13, R16 | 4 | 100k Ohms | 表面実装1005mm |  | YAGEO | RC0402FR-07100KL | 可 | https://www.digikey.jp/short/4j3v3bpp
抵抗 | R8, R11, R14, R17 | 5 | 10 Ohms 0.25W | 表面実装1608mm |  | Rohm Semiconductor | ESR03EZPF10R0 | 可 | https://www.digikey.jp/short/9bdf1988
抵抗 | R22 | 1 | 510 Ohms
スイッチ | SW1 | 1 | KMR211NGLFS |  |  | C&K | KMR211NGLFS | 可 | https://www.digikey.jp/short/tr7n1v4v
スイッチ | SW2 | 1 | SS12D01G4 |  |  | Switronic lndustrial Corp. | SS12D01G4 | 不可 | https://akizukidenshi.com/catalog/g/g112723/
ＩＣ | U1, U9 | 2 | MA730 | QFN-16 (3mmx3mm) | 向きがあるので、実装注意 (本ファイル別タブ「部品実装向き」参照) | Monolithic Power Systems Inc. | MA730GQ-Z | 不可 | https://www.digikey.jp/short/7brnh7h5
ＩＣ | U3 | 1 | DRV8836DSSR | 12-WFDFN | 向きがあるので、実装注意 (本ファイル別タブ「部品実装向き」参照) | Texas Instruments | DRV8836DSSR | 不可 | https://www.digikey.jp/short/qpjfthmj
ＩＣ | U4 | 1 | STM32F411CEU6/STM32F413CHU6 | 48-UFQFN | 向きがあるので、実装注意 (本ファイル別タブ「部品実装向き」参照) | STMicroelectronics | STM32F411CEU6 | 不可 | https://www.digikey.jp/short/2tf2bp12
ＩＣ | U7 | 1 | MCP73831 | SOT-23-5 |  | Microchip Technology | MCP73831T-2ACI/OT | 不可 | https://www.digikey.jp/short/c23d1f0r
ＩＣ | U8 | 1 | ICM-42688-P |  |  | TDK InvenSense | ICM-42688-P | 不可 | https://www.digikey.jp/short/dczjj7mt
ＩＣ | U11 | 1 | LP5907MFX-3.0 | SOT-23-5 |  | Texas Instruments | LP5907MFX-3.0/NOPB | 不可 | https://www.digikey.jp/short/rwd9d7jb
ＩＣ | U12 | 1 | STLINK-V3MOS |  |  | STMicroelectronics | STLINK-V3MODS | 不可 | https://www.digikey.jp/short/mr74wj20

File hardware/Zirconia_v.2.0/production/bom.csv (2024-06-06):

Designator | Footprint | Quantity | Value | LCSC Part #
C1, C11, C13, C16, C18, C4, C5, C8 | 0402 | 8 | 0.1u
C10, C12, C14, C15, C2, C20, C21, C6, C7, C9 | 0603 | 10 | 10u
C17 | 0402 | 1 | 10n
C19 | 0402 | 1 | 4.7u
D1, D3 | OSI5FU3A11C | 2 | OSI5FU3A11C
D10, D6 | 0603 | 2 | XL-1608SURC-06 | XL-1608SURC-06
D2, D4 | OSI5FU3A11C_Reverse | 2 | OSI5FU3A11C
D5 | 0603 | 1 | XL-1608UYC-06 | XL-1608UYC-06
D7 | 0603 | 1 | XL-1608SYGC-06 | XL-1608SYGC-06
D8, D9 | 0603 | 2 | XL-1608UBC-04 | XL-1608UBC-04
J1, J4 | PinHeader_2x05_P1.27mm_Vertical_SMD | 2 | BD125-10-A-0305-0580-L-B
J2 | PinSocket_1x04_P2.54mm_Vertical | 1 | Conn_01x04
L1, L2 | Inductor | 2 | 47uH | AMWPH4018S470MT
P1, P3 | motor_pin | 2 | Red
P2, P4 | motor_pin | 2 | Blk
P6 | Molex_PicoBlade_53047-0210_1x02_P1.25mm_Vertical | 1 | PicoBlade_53047-0210
Q1, Q2 | Phototransistor_D3.0mm_Horizontal_O1.27mm_Z2.0mm_IRBlack | 2 | LTR
Q3, Q4 | Phototransistor_D3.0mm_Horizontal_O1.27mm_Z2.0mm_IRBlack_Reverse | 2 | LTR
Q5, Q6, Q7, Q8 | SOT-23 | 4 | IRLML6344
Q9 | SOT-563 | 1 | DMC2400UV-7
R1, R12, R15, R2, R20, R21, R23, R24, R26, R3, R4, R6, R9 | 0402 | 13 | 1k
R10, R13, R16, R7 | 0402 | 4 | 100k
R11, R14, R17, R8 | 0603 | 4 | 10
R18, R19, R25, R27, R5 | 0402 | 5 | 10k
R22 | 0402 | 1 | 510
SW1 | KMR2xxNG_LFS | 1 | KMR211NG LFS
SW2 | SS12D01G4 | 1 | SS12D01G4
U1, U9 | MA302GQ-P | 2 | MA302/MA730
U10, U2 | ENC_CONN_VART | 2 | ENCODER_CONNECT_IC
U11 | SOT-23-5 | 1 | LP5907MFX-3.0
U12 | mod_stlink-v3m_mb1467 | 1 | STLINK-V3MOS
U3 | DRV8836DSSR | 1 | DRV8836DSSR
U4 | QFN-48-1EP_7x7mm_P0.5mm_EP5.6x5.6mm | 1 | STM32F411CEU6/STM32F413CHU6
U5, U6 | ENC_CONN_FLAT | 2 | ENCODER_CONNECT_PCB
U7 | SOT-23-5 | 1 | MCP73831T-2ACI/OT
U8 | ICM-42688-P_handsoldering | 1 | ICM-42688-P

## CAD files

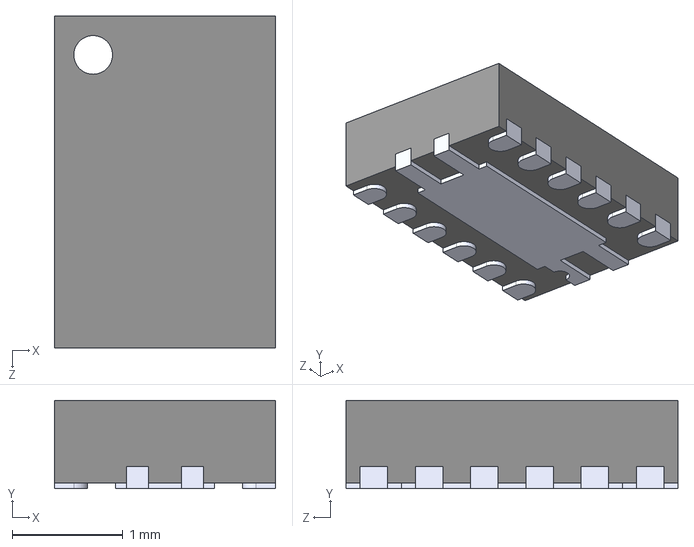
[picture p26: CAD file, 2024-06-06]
hardware/Zirconia_v.2.0/DRV8836DSSR/DRV8836DSSR.STEP
2.00 x 0.8 x 3.00 mm

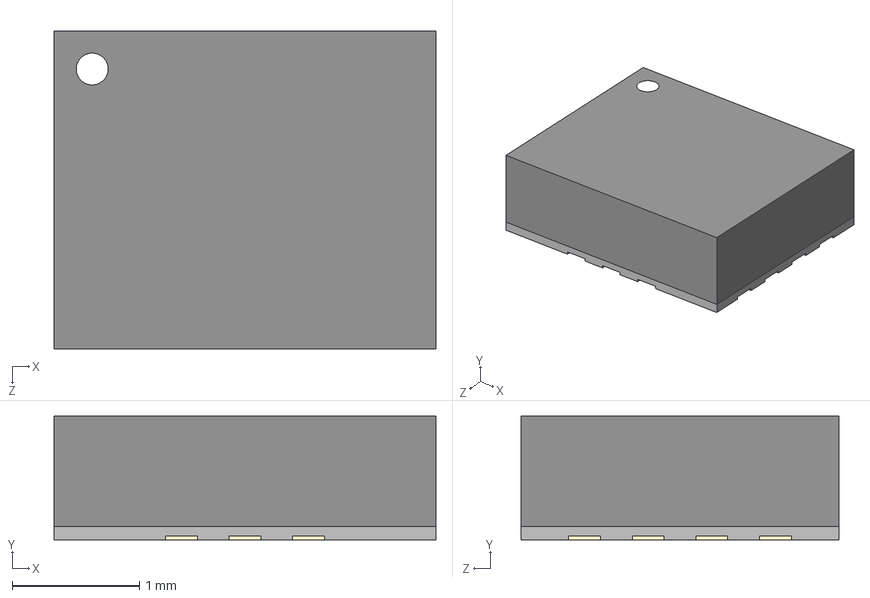
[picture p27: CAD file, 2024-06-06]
hardware/Zirconia_v.2.0/ICM-42688-P/ICM-42688-P.step
3.00 x 0.97 x 2.50 mm

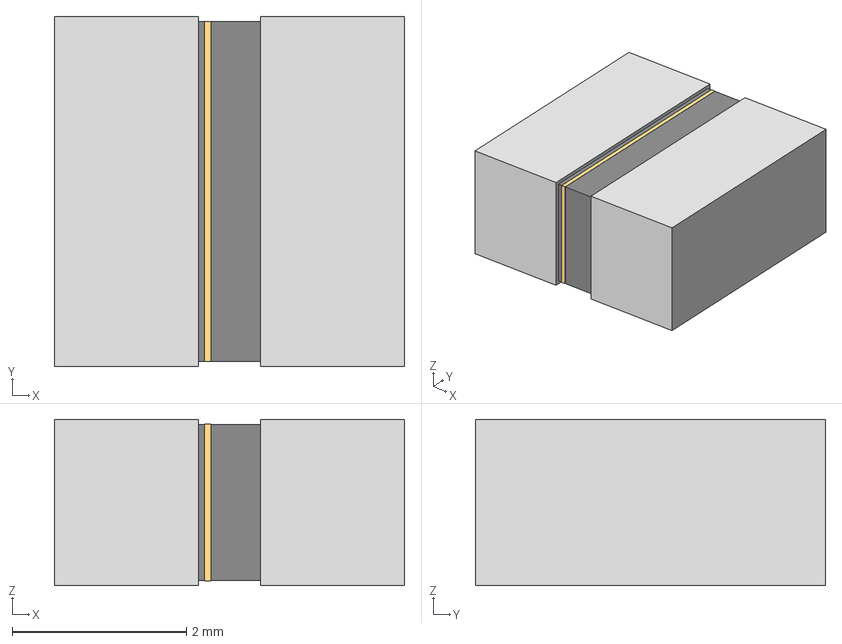
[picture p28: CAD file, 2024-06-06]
hardware/Zirconia_v.2.0/IFSC-1515AH-01/IND_IFSC_1515AH_VIS.step
4.01 x 4.01 x 1.91 mm

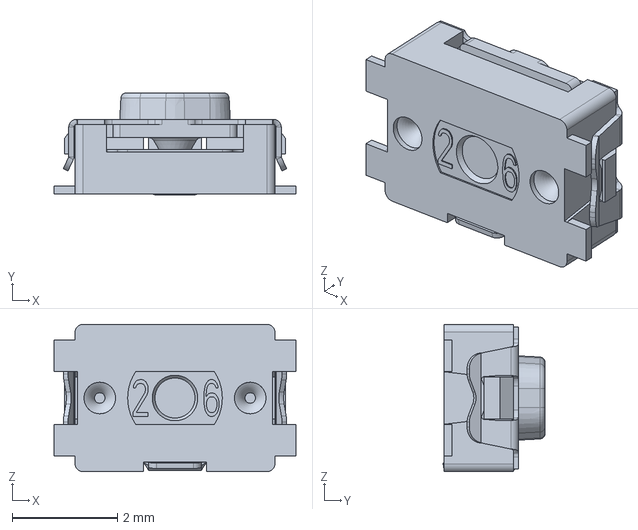
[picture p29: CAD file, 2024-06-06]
hardware/Zirconia_v.2.0/KMR211GLFS/KMR211GLFS.stp
4.60 x 1.94 x 2.80 mm

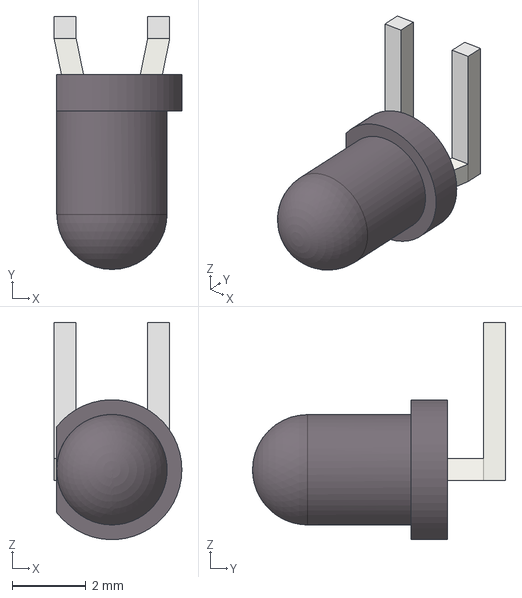
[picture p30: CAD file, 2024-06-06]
hardware/Zirconia_v.2.0/LTR-4206E/LTR-4206E_Reverse.stp
3.47 x 6.87 x 5.90 mm

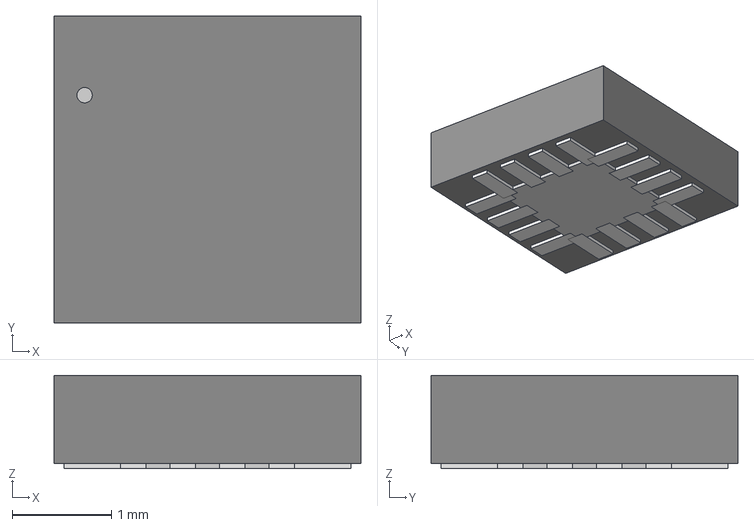
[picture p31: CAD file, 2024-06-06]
hardware/Zirconia_v.2.0/MA302GQ-P/QFN-3x3_MA302_MNP.step
3.10 x 3.10 x 0.942 mm

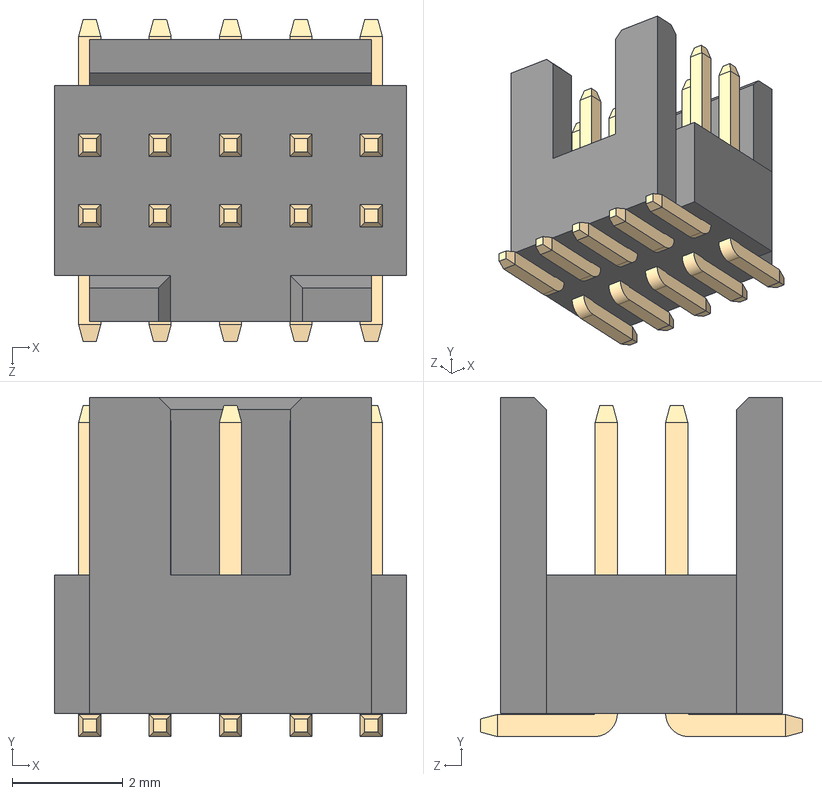
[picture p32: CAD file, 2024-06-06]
hardware/Zirconia_v.2.0/step/BD125-10-A-0305-0580-L-B.STEP
6.35 x 6.12 x 5.80 mm

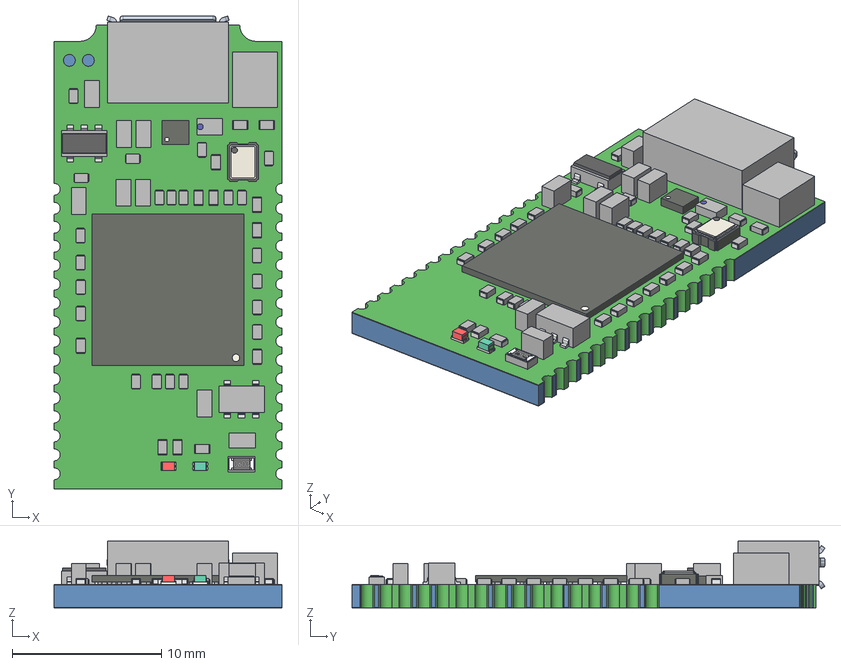
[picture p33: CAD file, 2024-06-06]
hardware/Zirconia_v.2.0/STLINK-V3MOS/STLINK-V3MODS.step
15.2 x 31.7 x 4.47 mm
Board
LED0402_greenH05
Extruded x 59
R0402 x 12
C0402 x 22
C0603 x 8
SOT23-5L x 2
LED0402_redH05
R0603

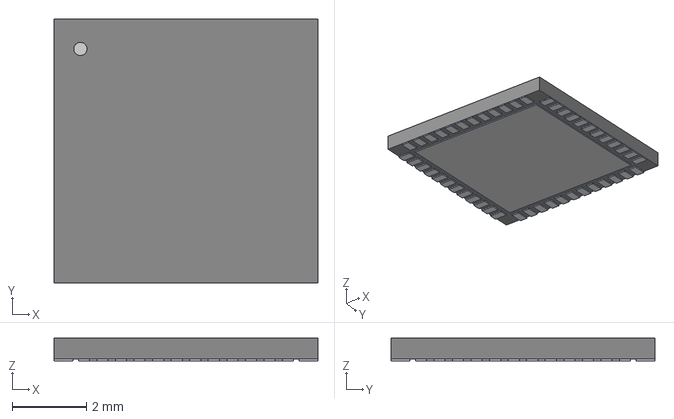
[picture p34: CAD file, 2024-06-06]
hardware/Zirconia_v.2.0/STM32F411CEU6/UFQFPN-48_7X7X0P55MM.step
7.11 x 7.11 x 0.612 mm

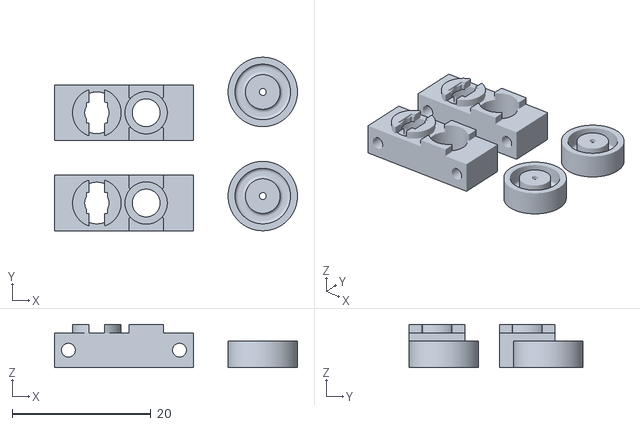
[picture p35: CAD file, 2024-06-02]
hardware/ZirconiaSTL_v.2.0.stl
35.0 x 25.0 x 6.20

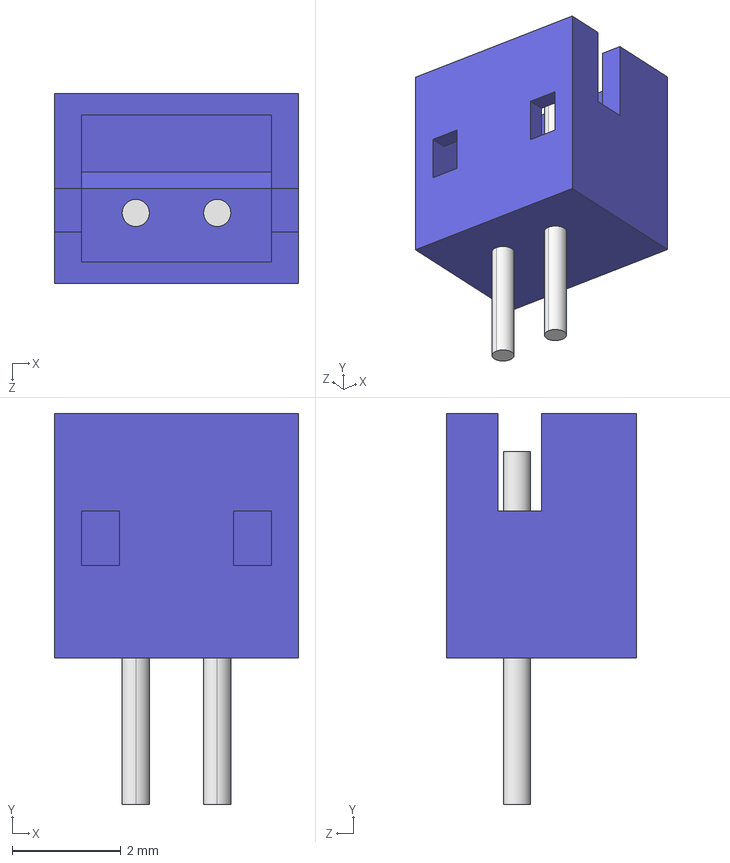
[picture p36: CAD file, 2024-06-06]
hardware/Zirconia_v.2.0/step/B2B-ZR.STEP
4.50 x 7.20 x 3.50 mm

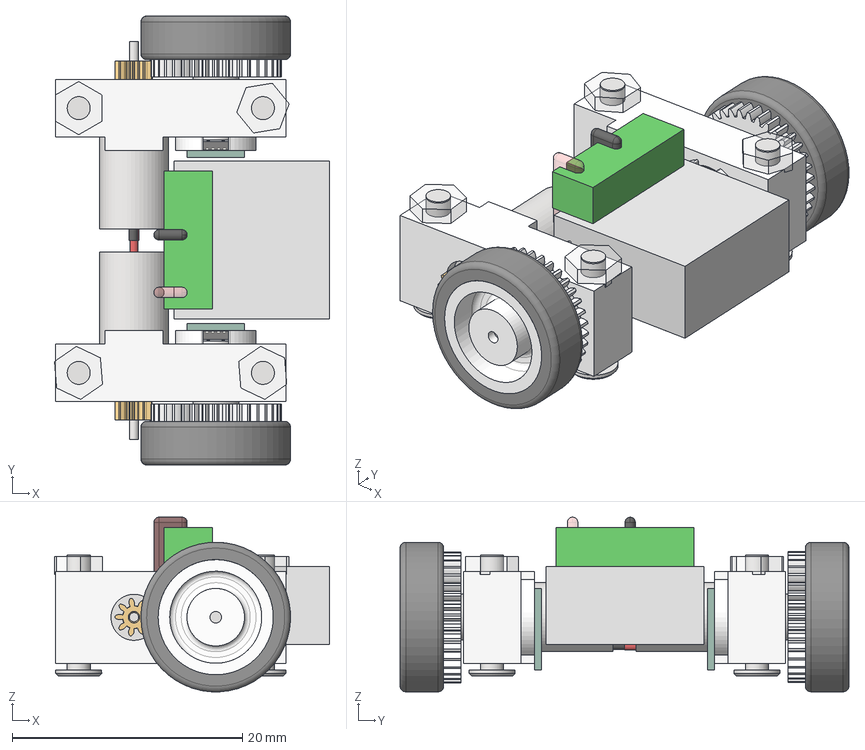
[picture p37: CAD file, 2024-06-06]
hardware/Zirconia_v.2.0/step/Zironia_mechanical.stp
23.9 x 39.0 x 15.2 mm
CorelessMotor_MK06-4.5 x 2
Tire_RT-MM_TIRE20 x 2
PinionGear_RT-PN x 2
スリムヘッド小ねじ(ステンレス) _41746731 x 4
M2六角ナット(ポリカーボネート) _EA945AP-201 x 4
Li-Po100mAh_FB19_改造
ミニチュア玉軸受両側鋼板シールド形内径3 外径6幅2.5_MR63ZZ x 4
GearM0.3Z38T1.5d3 x 2
平行ピン硬質(ステンレス) 3x8_42205283 x 2
3×4mmセットアップ・ステンレスシム0. 2mm厚_EG-SH3 x 2
ネオジム磁石(N40)円柱型Φ3x2(mm)径方向_ MAG17163612992482 x 2
WheelΦ3_20240130 x 2
MotorMountΦ3_20240414 x 2
MA730_board_1 x 2

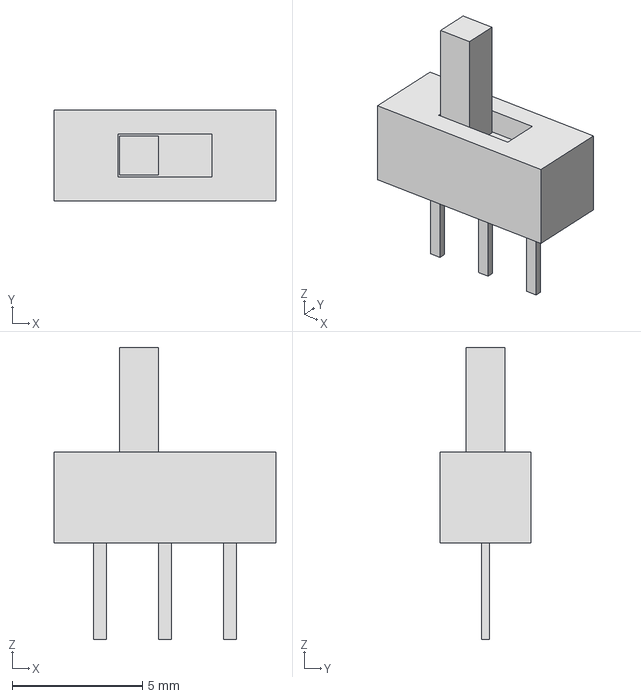
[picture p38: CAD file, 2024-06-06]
hardware/Zirconia_v.2.0/step/SS12D01G4.stp
8.50 x 3.50 x 11.2 mm

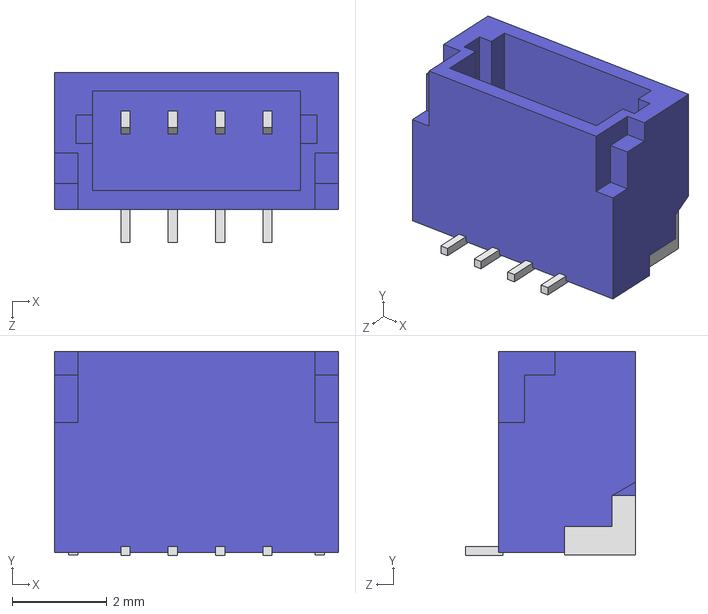
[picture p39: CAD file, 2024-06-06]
hardware/Zirconia_v.2.0/step/BM04B-SRSS-TB.STEP
6.00 x 4.32 x 3.60 mm

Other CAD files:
hardware/Zirconia_v.2.0/OSI5FU3A11C/OSI5FU3A11C_Reverse.stp
hardware/Zirconia_v.2.0/LTR-4206E/LTR-4206E.stp
hardware/Zirconia_v.2.0/OSI5FU3A11C/OSI5FU3A11C.stp
hardware/Zirconia_v.2.0/step/530470210.stp

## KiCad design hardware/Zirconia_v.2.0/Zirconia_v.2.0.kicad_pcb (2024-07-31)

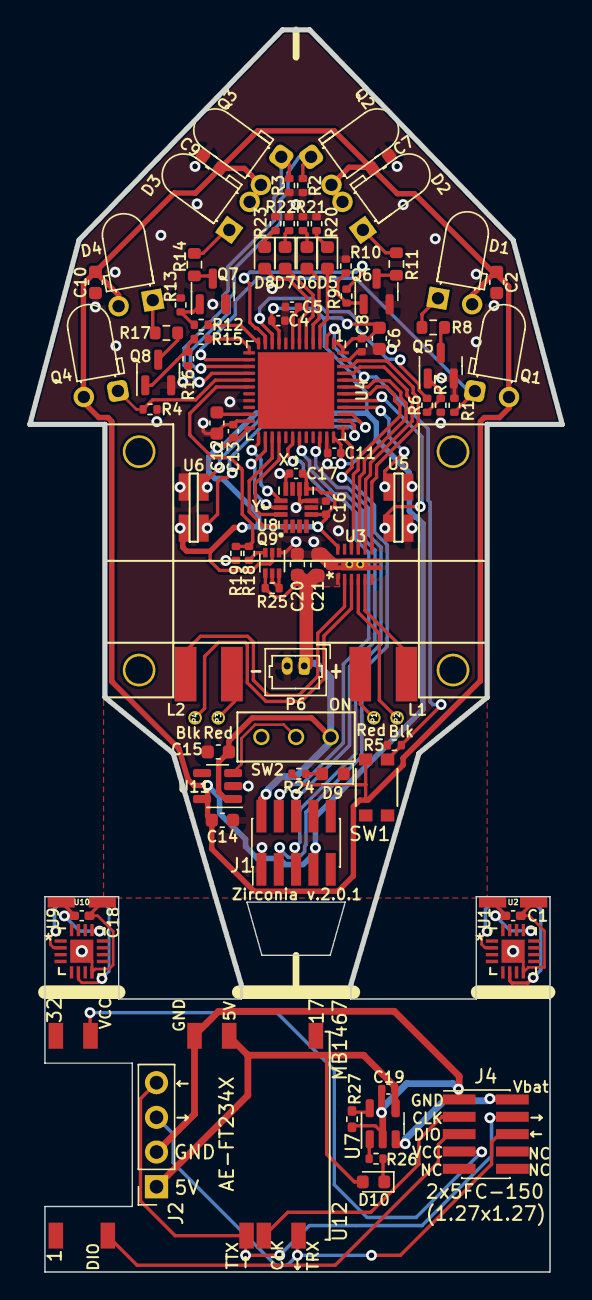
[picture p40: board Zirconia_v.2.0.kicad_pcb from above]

Board: 2 copper layers, 39.0 x 91.0 mm, 91 parts (0 on the bottom side), 80 nets.

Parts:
C1, C18: 0.1u; C_0402_1005Metric_Pad0.74x0.62mm_HandSolder
C2, C6, C7, C9, C10, C12, C14, C15, C20, C21: 10u; C_0603_1608Metric
C4, C5, C8, C11, C13, C16: 0.1u; C_0402_1005Metric
C17: 10n; C_0402_1005Metric
C19: 4.7u; C_0402_1005Metric
D1, D3: OSI5FU3A11C
D2, D4: OSI5FU3A11C; OSI5FU3A11C_Reverse
D5: XL-1608UYC-06; LED_0603_1608Metric
D6, D10: XL-1608SURC-06; LED_0603_1608Metric
D7: XL-1608SYGC-06; LED_0603_1608Metric
D8, D9: XL-1608UBC-04; LED_0603_1608Metric
J1, J4: BD125-10-A-0305-0580-L-B; PinHeader_2x05_P1.27mm_Vertical_SMD
J2: Conn_01x04; PinSocket_1x04_P2.54mm_Vertical
L1, L2: 47uH; Inductor
Mot_mount: V; Mot_mount
P1, P3: Red; motor_pin
P2, P4: Blk; motor_pin
P6: PicoBlade_53047-0210; Molex_PicoBlade_53047-0210_1x02_P1.25mm_Vertical
Q1, Q2: LTR; Phototransistor_D3.0mm_Horizontal_O1.27mm_Z2.0mm_IRBlack
Q3, Q4: LTR; Phototransistor_D3.0mm_Horizontal_O1.27mm_Z2.0mm_IRBlack_Re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
Q5, Q6, Q7, Q8: IRLML6344; SOT-23
Q9: DMC2400UV-7; SOT-563
R1, R2, R3, R4, R6, R9, R12, R15, R20, R21, R23, R24, R26: 1k; R_0402_1005Metric
R5, R18, R19, R25: 10k; R_0402_1005Metric
R7, R10, R13, R16: 100k; R_0402_1005Metric
R8, R11, R14, R17: 10; R_0603_1608Metric
R22: 510; R_0402_1005Metric
R27: 10k; R_0402_1005Metric_Pad0.72x0.64mm_HandSolder
SW1: KMR211NG LFS; KMR2xxNG_LFS
SW2: SS12D01G4
U1, U9: MA302/MA730; MA302GQ-P
U2, U10: ENCODER_CONNECT_IC; ENC_CONN_VART
U3: DRV8836DSSR
U4: STM32F411CEU6/STM32F413CHU6; QFN-48-1EP_7x7mm_P0.5mm_EP5.6x5.6mm
U5, U6: ENCODER_CONNECT_PCB; ENC_CONN_FLAT
U7: MCP73831T-2ACI/OT; SOT-23-5
U8: ICM-42688-P; ICM-42688-P_handsoldering
U11: LP5907MFX-3.0; SOT-23-5
U12: STLINK-V3MOS; mod_stlink-v3m_mb1467

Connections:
+3V0: C2.1, C4.1, C6.1, C7.1, C8.1, C9.1, C10.1, C11.1, C13.1, C14.1, C16.1, C17.1, D1.2 (A), D2.2 (A), D3.2 (A), D4.2 (A), J1.7, Q1.2 (C), Q2.2 (C), Q3.2 (C), Q4.2 (C), Q9.2 (G), R24.2, SW1.2, U3.12 (NSLEEP), U4.1 (VBAT), U4.9 (VDDA/VREF+), U4.24 (VDD), U4.36 (VDD), U4.48 (VDD), U5.1 (VCC), U6.1 (VCC), U8.5 (VDDIO), U8.8 (VDD), U11.5 (OUT)
+BATT: C15.1, C20.1, C21.1, J1.2, P6.1, Q9.4 (S), R25.1, SW2.1 (A), U3.1 (VCC), U11.1 (IN)
GND: C2.2, C4.2, C5.2, C6.2, C7.2, C8.2, C9.2, C10.2, C11.2, C12.2, C13.2, C14.2, C15.2, C16.2, C17.2, C20.2, C21.2, D9.1 (K), J1.1, P6.2, Q5.2 (S), Q6.2 (S), Q7.2 (S), Q8.2 (S), Q9.1 (S), R1.2, R2.2, R3.2, R4.2, R5.2, R7.2, R10.2, R13.2, R16.2, R19.2, R20.1, R21.1, R22.1, R23.1, U3.6 (GND), U3.13 (EPAD), U4.8 (VSSA/VREF-), U4.20 (PB2/BOOT1), U4.23 (VSS), U4.35 (VSS), U4.47 (VSS), U5.2 (GND), U6.2 (GND), U8.6 (GND), U8.7 (RESV_7), U8.9 (INT2/FSYNC/CLKIN), U8.11 (RESV_11), U11.2 (GND)
unnamed: D1.1 (K), R8.1
unnamed: D2.1 (K), R11.1
unnamed: D3.1 (K), R14.1
unnamed: D4.1 (K), R17.1
unnamed: D5.2 (A), U4.3 (PC14/OSC32-IN)
unnamed: D5.1 (K), R20.2
unnamed: D6.2 (A), U4.4 (PC15/OSC32-OUT)
unnamed: D6.1 (K), R21.2
unnamed: D7.2 (A), U4.5 (PH0/OSC-IN)
unnamed: D7.1 (K), R22.2
unnamed: D8.2 (A), U4.6 (PH1/OSC-OUT)
unnamed: D8.1 (K), R23.2
unnamed: D9.2 (A), R24.1
unnamed: C19.1, D10.2 (A), J2.1, U7.4 (V_{DD}), U12.22 (5V_OPT)
unnamed: D10.1 (K), R26.2
unnamed: J1.3, U4.37 (PA14/SWCLK)
unnamed: J1.4, U4.30 (PA9/USART1TX)
unnamed: J1.5, U4.34 (PA13/SWDIO)
unnamed: J1.6, U4.31 (PA10/USRAT1RX)
unnamed: C19.2, J2.2, J4.1, R27.2, U7.2 (V_{SS}), U12.24 (GND)
unnamed: J2.3, J4.6, U12.15 (T_VCP_RX)
unnamed: J2.4, J4.4, U12.12 (T_VCP_TX)
unnamed: J4.2, U7.3 (V_{BAT})
unnamed: J4.3, U12.13 (T_JCLK/T_SWCLK)
unnamed: J4.5, U12.4 (T_JTMS/T_SWDIO)
unnamed: J4.7, U12.30 (T_VCC)
unnamed: L1.1, P1.1
unnamed: L2.1, P3.1
unnamed: Q1.1 (E), R1.1, U4.14 (PA4/ADC1-4)
unnamed: Q2.1 (E), R2.1, U4.15 (PA5/TIM2-1/SPI1SCK/ADC1-5)
unnamed: Q3.1 (E), R3.1, U4.16 (PA6/TIM3-1/SPI1MISO/ADC1-6)
unnamed: Q4.1 (E), R4.1, U4.17 (PA7/TIM3-2/SPI1MOSI/ADC1-7)
unnamed: Q5.3 (D), R8.2
unnamed: Q5.1 (G), R6.2, R7.1
unnamed: Q6.3 (D), R11.2
unnamed: Q6.1 (G), R9.2, R10.1
unnamed: Q7.3 (D), R14.2
unnamed: Q7.1 (G), R12.2, R13.1
unnamed: Q8.3 (D), R17.2
unnamed: Q8.1 (G), R15.2, R16.1
unnamed: Q9.5 (G), Q9.6 (D), R25.2
unnamed: Q9.3 (D), R18.1
unnamed: SW2.2 (B), U11.3 (EN)
unnamed: U1.2 (A), U2.3 (A)
unnamed: U1.6 (B), U2.4 (B)
unnamed: C1.1, U1.8 (GND), U1.17 (PAD), U2.2 (GND)
unnamed: C1.2, U1.13 (VDD), U2.1 (VCC)
unnamed: U3.10 (AIN1/APHASE), U4.42 (PB6/TIM4-1)
unnamed: U3.9 (AIN2/AENBL), U4.43 (PB7/TIM4-2)
unnamed: L2.2, U3.2 (AOUT1)
unnamed: P4.1, U3.3 (AOUT2)
unnamed: U3.8 (BIN1/BPHASE), U4.45 (PB8/TIM4-3)
unnamed: U3.7 (BIN2/BENBL), U4.46 (PB9/TIM4-4)
unnamed: P2.1, U3.4 (BOUT1)
unnamed: L1.2, U3.5 (BOUT2)
unnamed: R5.1, SW1.1, U4.2 (PC13), U4.44 (BOOT0)
unnamed: C5.1, U4.7 (NRST)
unnamed: R6.1, U4.10 (PA0/TIM2-1,5-1/ADC1-0)
unnamed: R9.1, U4.11 (PA1/TIM2-2,5-2/ADC1-1)
unnamed: R12.1, U4.12 (PA2/TIM2-3,5-3/ADC1-2)
unnamed: R15.1, U4.13 (PA3/TIM2-4,5-4/ADC1-3)
unnamed: U4.38 (PA15/TIM2-1), U6.3 (A)
unnamed: R18.2, R19.1, U4.18 (PB0/TIM3-3/ADC1-8)
unnamed: U4.39 (PB3/TIM2-2/SPI1SCK/SPI3SCK), U6.4 (B)
unnamed: U4.40 (PB4/TIM3-1/SPI1MISO/SPI3MISO), U5.3 (A)
unnamed: U4.41 (PB5/TIM3-2/SPI1MOSI/SPI3MOSI), U5.4 (B)
unnamed: U4.25 (PB12/SPI3SCK), U8.12 (AP_CS)
unnamed: U4.26 (PB13/SPI2SCK), U8.13 (AP_SCL/AP_SCLK)
unnamed: U4.27 (PB14/SPI2MISO), U8.1 (AP_SDO/AP_AD0)
unnamed: U4.28 (PB15/SPI2MOSI), U8.14 (AP_SDA/AP_SDIO/AP_SDI)
unnamed: C12.1, U4.22 (VCAP1)
unnamed: R27.1, U7.5 (PROG)
unnamed: R26.1, U7.1 (STAT)
unnamed: U9.2 (A), U10.3 (A)
unnamed: U9.6 (B), U10.4 (B)
unnamed: C18.1, U9.8 (GND), U9.17 (PAD), U10.2 (GND)
unnamed: C18.2, U9.13 (VDD), U10.1 (VCC)

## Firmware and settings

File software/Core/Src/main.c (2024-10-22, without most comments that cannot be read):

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
/* Includes ------------------------------------------------------------------*/
#include "main.h"

#include "adc.h"
#include "dma.h"
#include "gpio.h"
#include "spi.h"
#include "tim.h"
#include "usart.h"

/* USER CODE BEGIN Includes */
#include "module_index.h"
/* USER CODE END Includes */


void SystemClock_Config(void);
/**
 * @brief  The application entry point.
 * @retval int
 */
int main(void) {
    /* MCU Configuration--------------------------------------------------------*/

    /* Reset of all peripherals, Initializes the Flash interface and the Systick.
     */
    HAL_Init();

    /* Configure the system clock */
    SystemClock_Config();

    /* Initialize all configured peripherals */
    MX_GPIO_Init();
    MX_DMA_Init();
    MX_USART1_UART_Init();
    MX_ADC1_Init();
    MX_TIM1_Init();
    MX_TIM2_Init();
    MX_TIM3_Init();
    MX_TIM4_Init();
    MX_TIM5_Init();
    MX_SPI2_Init();
    /* USER CODE BEGIN 2 */
    LED_ALL_ON();              // LED全点灯
    Communicate_Initialize();
    Motor_Initialize();
    Encoder_Initialize();
    IMU_Initialize();
    Sensor_Initialize();
    Interrupt_Initialize();
    Myshell_Initialize();

    Battery_LimiterVoltage();
    module_test();
    /* USER CODE END 2 */

    /* Infinite loop */
    /* USER CODE BEGIN WHILE */

    float target_straight_velocity = 0;  // 目標速度[ms^-1]
    float target_rotate_velocity = 0;
    float current_straight_velocity;
    float current_rotate_velocity;
    float TIRE_RADIUS = 13 / 2;  // タイヤの半径[mm]

    float pid_straight_proportional_diff = 0;
    float pid_straight_integral_diff = 0;
    float pid_straight_differential_diff = 0;
    float pid_straight_differential_diff_before = 0;

    float pid_rotate_proportional_diff = 0;
    float pid_rotate_integral_diff = 0;
    float pid_rotate_differential_diff = 0;
    float pid_rotate_differential_diff_before = 0;

    float Kp_straight = 3, Ki_straight = 0, Kd_straight = 0;
    float Kp_rotate = 0, Ki_rotate = 0, Kd_rotate = 0;

    float duty_l = 0, duty_r = 0;  // dutyは0~1000 "Module\src\motor.c"

    while (1) {
        /* USER CODE END WHILE */

        /* USER CODE BEGIN 3 */

        // Myshell_Execute();

        // 1. 現在速を計算する

        current_straight_velocity = TIRE_RADIUS * (Encoder_GetAngle_Left() + Encoder_GetAngle_Right()) / 2;  // mm/ms
        current_rotate_velocity = IMU_GetGyro_Z();                                                           // rad/s

        // 2. 目標との差分を計算する
        pid_straight_proportional_diff = target_straight_velocity - current_straight_velocity;
        pid_straight_integral_diff += pid_straight_proportional_diff;
        pid_straight_differential_diff = pid_straight_differential_diff_before - pid_straight_proportional_diff;
        pid_straight_differential_diff_before = pid_straight_differential_diff;

        pid_rotate_proportional_diff = target_rotate_velocity - current_rotate_velocity;
        pid_rotate_integral_diff += pid_rotate_proportional_diff;
        pid_rotate_differential_diff = pid_rotate_differential_diff_before - pid_rotate_proportional_diff;
        pid_rotate_differential_diff_before = pid_rotate_differential_diff;

        // 3. PID制御 右が正
        duty_r = Kp_straight * pid_straight_proportional_diff + Ki_straight * pid_straight_integral_diff +
                 Kd_straight * pid_straight_differential_diff +
                 (Kp_rotate * pid_rotate_proportional_diff + Ki_rotate * pid_rotate_integral_diff + Kd_rotate * pid_rotate_differential_diff);
        duty_l = Kp_straight * pid_straight_proportional_diff + Ki_straight * pid_straight_integral_diff +
                 Kd_straight * pid_straight_differential_diff -
                 (Kp_rotate * pid_rotate_proportional_diff + Ki_rotate * pid_rotate_integral_diff + Kd_rotate * pid_rotate_differential_diff);

        duty_r = SIGN(duty_r) * MIN(950, ABS(duty_r));
        duty_l = SIGN(duty_l) * MIN(950, ABS(duty_l));

        // 4. Dutyをつっこむ
        Motor_SetDuty_Left(duty_l);
        Motor_SetDuty_Right(duty_r);

        // 5. 制御周期は1msだから1msまつ
        HAL_Delay(1);
    }
    /* USER CODE END 3 */
}

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


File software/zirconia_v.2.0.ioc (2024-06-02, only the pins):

Mcu.UserName=STM32F411CEUx
PA0-WKUP.GPIO_Label=LED_FR
PA0-WKUP.Signal=GPIO_Output
PA1.GPIO_Label=LED_SR
PA1.Signal=GPIO_Output
PA10.Signal=USART1_RX
PA13.Signal=SYS_JTMS-SWDIO
PA14.Signal=SYS_JTCK-SWCLK
PA15.Signal=S_TIM2_CH1_ETR
PA2.GPIO_Label=LED_SL
PA2.Signal=GPIO_Output
PA3.GPIO_Label=LED_FL
PA3.Signal=GPIO_Output
PA4.GPIO_Label=SEN_FR
PA4.Signal=ADCx_IN4
PA5.GPIO_Label=SEN_SR
PA5.Signal=ADCx_IN5
PA6.GPIO_Label=SEN_SL
PA6.Signal=ADCx_IN6
PA7.GPIO_Label=SEN_FL
PA7.Signal=ADCx_IN7
PA9.Signal=USART1_TX
PB0.GPIO_Label=V_BAT
PB0.Signal=ADCx_IN8
PB12.GPIO_Label=SPI2_CS
PB12.Signal=GPIO_Output
PB13.Signal=SPI2_SCK
PB14.Signal=SPI2_MISO
PB15.Signal=SPI2_MOSI
PB3.Signal=S_TIM2_CH2
PB4.Signal=S_TIM3_CH1
PB5.Signal=S_TIM3_CH2
PB6.GPIO_Label=MOT_RF
PB6.Signal=S_TIM4_CH1
PB7.GPIO_Label=MOT_RR
PB7.Signal=S_TIM4_CH2
PB8.GPIO_Label=MOT_LF
PB8.Signal=S_TIM4_CH3
PB9.GPIO_Label=MOT_LR
PB9.Signal=S_TIM4_CH4
PC13-ANTI_TAMP.GPIO_Label=SWITCH
PC13-ANTI_TAMP.Signal=GPIO_Input
PC14-OSC32_IN.GPIO_Label=LED_YELLOW
PC14-OSC32_IN.Signal=GPIO_Output
PC15-OSC32_OUT.GPIO_Label=LED_RED
PC15-OSC32_OUT.Signal=GPIO_Output

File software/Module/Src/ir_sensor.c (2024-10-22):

/**
 * Copyright 2020 kohiro
 *
 * Licensed under the Apache License, Version 2.0 (the "License");
 * you may not use this file except in compliance with the License.
 * You may obtain a copy of the License at
 *
 *     http://www.apache.org/licenses/LICENSE-2.0
 *
 * Unless required by applicable law or agreed to in writing, software
 * distributed under the License is distributed on an "AS IS" BASIS,
 * WITHOUT WARRANTIES OR CONDITIONS OF ANY KIND, either express or implied.
 * See the License for the specific language governing permissions and
 * limitations under the License.
 */

#include "module_index.h"

typedef enum {
    BATTERY_0 = 0,
    BATTERY_1 = 1,
    LED_FR_OFF = 2,
    LED_FR_ON = 3,
    LED_FL_OFF = 4,
    LED_FL_ON = 5,
    LED_SR_OFF = 6,
    LED_SR_ON = 7,
    LED_SL_OFF = 8,
    LED_SL_ON = 9,
    BATTERY_2 = 10,
    BATTERY_3 = 11,
    NUM_ADC,
} t_sensor_mode;

volatile static uint32_t led_on_pattern[NUM_ADC] = {0};  // LED点灯コマンド
volatile static uint32_t led_off_pattern = 0x000F0000;   // LED消灯コマンド
volatile static uint16_t adc_value[NUM_ADC];             // AD変換値

// 割り込み内の処理を記述した関数群
extern void Interrupt_Main(void);
extern void Interrupt_PreProcess(void);
extern void Interrupt_PostProcess(void);

/* ---------------------------------------------------------------
        全AD変換終了後に行われる割り込み関数(Don't change the function name)
--------------------------------------------------------------- */
void HAL_ADC_ConvCpltCallback(ADC_HandleTypeDef* hadc) {
    Interrupt_PreProcess();
    Interrupt_Main();
    Interrupt_PostProcess();
}

/* ---------------------------------------------------------------
        赤外センサの出力設定関数
--------------------------------------------------------------- */
void Sensor_TurnOffLED(void) {
    for (int8_t i = 0; i < NUM_ADC; i++) {
        led_on_pattern[i] = 0;
    }
}

void Sensor_TurnOnLED(void) {
    Sensor_TurnOffLED();
    led_on_pattern[LED_FL_ON] = LED_FL_Pin;
    led_on_pattern[LED_SL_ON] = LED_SL_Pin;
    led_on_pattern[LED_SR_ON] = LED_SR_Pin;
    led_on_pattern[LED_FR_ON] = LED_FR_Pin;
}

/* ---------------------------------------------------------------
        赤外センサの初期設定関数
--------------------------------------------------------------- */
void Sensor_Initialize(void) {
    htim1.Instance->DIER |= TIM_DIER_CC1DE | TIM_DIER_CC2DE;
    __HAL_TIM_MOE_ENABLE(&htim1);
    __HAL_TIM_CLEAR_FLAG(&htim1, TIM_FLAG_UPDATE);

    HAL_DMA_Start_IT(htim1.hdma[TIM_DMA_ID_CC1], (uint32_t)led_on_pattern, (uint32_t)(&(GPIOA->BSRR)), NUM_ADC);
    HAL_DMA_Start_IT(htim1.hdma[TIM_DMA_ID_CC2], (uint32_t)(&led_off_pattern), (uint32_t)(&(GPIOA->BSRR)), 1);
    HAL_ADC_Start_DMA(&hadc1, (uint32_t*)adc_value, NUM_ADC);
    HAL_TIM_PWM_Start(&htim1, TIM_CHANNEL_1);
    HAL_TIM_PWM_Start(&htim1, TIM_CHANNEL_2);
    HAL_TIM_PWM_Start(&htim1, TIM_CHANNEL_3);
}

/* ---------------------------------------------------------------
        バッテリのAD値を取得する関数
--------------------------------------------------------------- */
uint16_t Sensor_GetBatteryValue(void) {
    return ((adc_value[BATTERY_0] + adc_value[BATTERY_1] + adc_value[BATTERY_2] + adc_value[BATTERY_3]) / 4);
}

/* ---------------------------------------------------------------
        赤外センサの偏差値を取得する関数
--------------------------------------------------------------- */
int16_t Sensor_GetValue(uint8_t dir) {
    switch (dir) {
        case 3:
            return adc_value[LED_FL_ON] - adc_value[LED_FL_OFF];
            break;
        case 2:
            return adc_value[LED_SL_ON] - adc_value[LED_SL_OFF];
            break;
        case 0:
            return adc_value[LED_SR_ON] - adc_value[LED_SR_OFF];
            break;
        case 1:
            return adc_value[LED_FR_ON] - adc_value[LED_FR_OFF];
            break;
        default:
            return -1;
            break;
    }
}

/* ---------------------------------------------------------------
        デバッグ用
--------------------------------------------------------------- */
void Sensor_DebugPrintf(void) {
    Sensor_TurnOnLED();
    while (Communicate_Receice1byte() != _ESC) {
        printf("%5d (%4d - %3d), %5d (%4d - %3d), %5d (%4d - %3d), %5d (%4d - %3d)\r\n", adc_value[LED_FL_ON] - adc_value[LED_FL_OFF],
               adc_value[LED_FL_ON], adc_value[LED_FL_OFF], adc_value[LED_SL_ON] - adc_value[LED_SL_OFF], adc_value[LED_SL_ON], adc_value[LED_SL_OFF],
               adc_value[LED_SR_ON] - adc_value[LED_SR_OFF], adc_value[LED_SR_ON], adc_value[LED_SR_OFF],
               adc_value[LED_FR_ON] - adc_value[LED_FR_OFF], adc_value[LED_FR_ON], adc_value[LED_FR_OFF]);

        /*		printf("%5d", adc_value[0]);
                        for(uint8_t i = 1; i < sizeof(adc_value) / sizeof(adc_value[0]); i++) {
                                printf(" ,%5d", adc_value[i]);
                        }
                        printf("\r\n");
        */
        HAL_Delay(100);
    }
    Sensor_TurnOffLED();
}

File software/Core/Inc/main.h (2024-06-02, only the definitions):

#define SWITCH_Pin GPIO_PIN_13
#define SWITCH_GPIO_Port GPIOC
#define LED_YELLOW_Pin GPIO_PIN_14
#define LED_YELLOW_GPIO_Port GPIOC
#define LED_RED_Pin GPIO_PIN_15
#define LED_RED_GPIO_Port GPIOC
#define LED_GREEN_Pin GPIO_PIN_0
#define LED_GREEN_GPIO_Port GPIOH
#define LED_BLUE_Pin GPIO_PIN_1
#define LED_BLUE_GPIO_Port GPIOH
#define LED_FR_Pin GPIO_PIN_0
#define LED_FR_GPIO_Port GPIOA
#define LED_SR_Pin GPIO_PIN_1
#define LED_SR_GPIO_Port GPIOA
#define LED_SL_Pin GPIO_PIN_2
#define LED_SL_GPIO_Port GPIOA
#define LED_FL_Pin GPIO_PIN_3
#define LED_FL_GPIO_Port GPIOA
#define SEN_FR_Pin GPIO_PIN_4
#define SEN_FR_GPIO_Port GPIOA
#define SEN_SR_Pin GPIO_PIN_5
#define SEN_SR_GPIO_Port GPIOA
#define SEN_SL_Pin GPIO_PIN_6
#define SEN_SL_GPIO_Port GPIOA
#define SEN_FL_Pin GPIO_PIN_7
#define SEN_FL_GPIO_Port GPIOA
#define V_BAT_Pin GPIO_PIN_0
#define V_BAT_GPIO_Port GPIOB
#define SPI2_CS_Pin GPIO_PIN_12
#define SPI2_CS_GPIO_Port GPIOB
#define MOT_RF_Pin GPIO_PIN_6
#define MOT_RF_GPIO_Port GPIOB
#define MOT_RR_Pin GPIO_PIN_7
#define MOT_RR_GPIO_Port GPIOB
#define MOT_LF_Pin GPIO_PIN_8
#define MOT_LF_GPIO_Port GPIOB
#define MOT_LR_Pin GPIO_PIN_9
#define MOT_LR_GPIO_Port GPIOB

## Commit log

2020-04-13 readmeの追加と細かいバグの修正
2020-04-13 readmeの追加と細かい修正
    [Zirconia-all-pos.csv, Zirconia-all-pos.xlsx, Zirconia.drl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]
2020-04-13 文字化け対策
2020-04-19 CubeIDE対応
2020-04-19 マニュアル更新
2022-04-04 ライセンスの追加
2022-07-31 フォルダ構成の変更
2022-07-31 開発環境のバージョンアップ
2022-07-31 DMA割込みの優先順位変更
2022-07-31 割込処理割合のオーバーフロー対策
2022-07-31 フラッシュ機能の実装
2022-07-31 readmeの修正
2023-08-14 IMUが1度しか更新されないバグの修正
2023-08-14 光センサ位置の表示修正
2023-08-17 最適化対策とリファクタリング
2024-06-02 update bom
    [Zirconia_v.2.0 部品リスト.xlsx]
2024-06-06 add AE-FT234X
    [530470210.stp, B2B-ZR.STEP, BD125-10-A-0305-0580-L-B.STEP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]
2024-07-31 JLCPCBパーツ反映
    [ST-LINK Board.kicad_sch, Zirconia_v.2.0 部品リスト.xlsx, Zirconia_v.2.0.kicad_pcb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]
2024-10-08 WIP: 宴会芸
2024-10-09 Linux + arm-none-eabi でビルドできるように
2024-10-22 WindowsでMakeを使ってコンパイルが通るようになった

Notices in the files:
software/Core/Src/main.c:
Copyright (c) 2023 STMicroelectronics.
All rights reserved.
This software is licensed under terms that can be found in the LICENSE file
